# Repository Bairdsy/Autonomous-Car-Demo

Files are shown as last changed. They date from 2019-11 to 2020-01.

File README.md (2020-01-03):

# Automous Car Demo

SAS Computer Vision demo with 3d printed autonomous car platform.  The sub-folders in this repository contain everything you need to know to build the demo, other than the building of the models / preparation of the Astores.
  - Astore Switcher :  The GUI for swapping the Astore and restarting the ESP server
  - Car Code : The autonomous navigation code running on the vehicle
  - Control Code : The code running on the control Raspberry Pi, which manages the lights, monitors and sensors
  - Electronics : How to setup the Raspberry Pi Zero W, Explorer Phat, Operating System and required modules (e.g. mjpg streamer)
  - ESP Server:  Containing the deployment & install scripts for setting up the ESP server on a virtual machine
  - Hardware : Instructions for building the car model frame and chassis
  - Images : Images used in the instructions

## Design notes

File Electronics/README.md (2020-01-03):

#Electronics Setup & Install
## Raspberry Pi OS Install 
1. In a web browser, navigate to the URL http://downloads.raspberrypi.org/raspbian/images/raspbian-2018-11-15/ and download the zip file 2018-11-13-raspbian-stretch.zip
2. Download and install the latest version of Balena Etcher for your desktop operating system from https://www.balena.io/etcher/
3. Run Balena Etcher
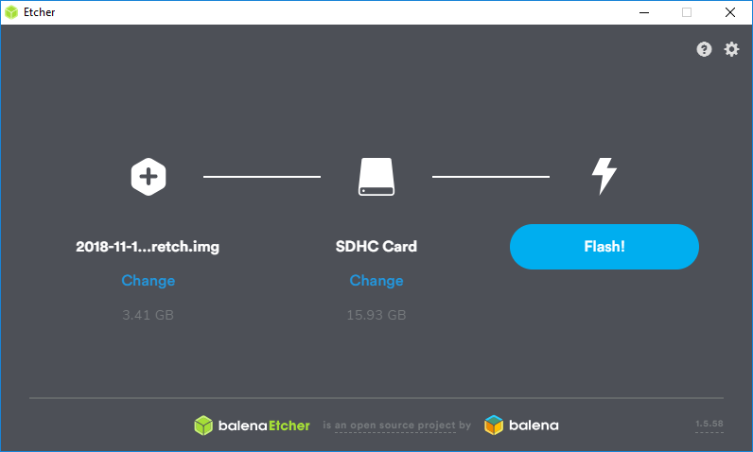
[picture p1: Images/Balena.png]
Etcher Screenshot
  
4. Click on “Select Image” and select the Raspbian Stretch zip file you downloaded.
5. Insert your microSD card into the slot on your computer (or a USB microSD reader if you don’t have a slot)
6. Click on “Flash!” 
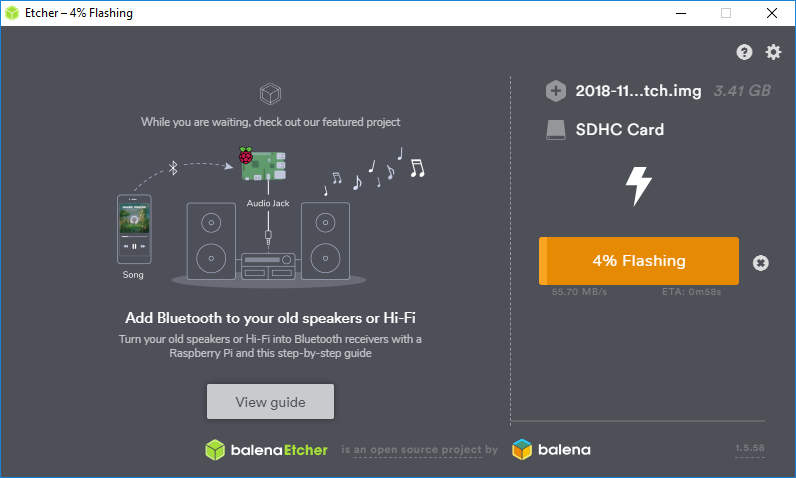
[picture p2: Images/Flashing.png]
Flashing
  
7. Wait for Balena Etcher to finish “Flashing” and “Verifying”.  Close any windows that pop up during this process giving warnings about drives that need formatting.
8. Remove the microSD card from your computer and insert it into the slot on the Raspberry Pi Zero W
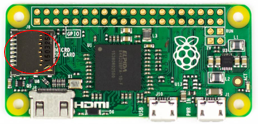
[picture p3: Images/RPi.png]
Raspberry Pi
  

## Explorer Phat
1.  The explorer Phat plugs into the top of the Raspberry Pi board as pictured
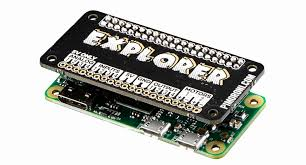
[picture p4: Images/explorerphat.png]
Explorer
  
2. Connect each of the 2 motors to the Motor 1 + and - and Motor 2 + and - connectors on the board
3. Connect the IR distance sensor to the Ground, Analog and 5V connectors

## Video Streaming Service
### Update & Install Tools
```
sudo apt-get update -y
sudo apt-get upgrade -y
sudo apt-get install build-essential imagemagick libv4l-dev libjpeg-dev cmake -y```
```

### Clone Repo in /tmp
```
cd /tmp
git clone https://github.com/jacksonliam/mjpg-streamer.git
cd mjpg-streamer/mjpg-streamer-experimental
```

### Make
```
make
sudo make install
```

### Run
```
/usr/local/bin/mjpg_streamer -i "input_uvc.so -r 1280x720 -d /dev/video0 -f 30" -o "output_http.so -p 8080 -w /usr/local/share/mjpg-streamer/www"
```

## Python Libraries
```
pip3 install scikit-learn
pip3 install scikit-image
sudo apt-get install python-opencv
sudo apt-get install python3-opencv
git clone http://github.com/pimoroni/explorer-hat
cd explorer-hat/library
sudo python setup.py install
```

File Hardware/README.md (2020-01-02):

# Hardware:
## Bill of Materials:
### For the Vehicle
| Number | Item | Indicative Cost |
| --- | --- | --- |
| 1 | Raspberry Pi Zero W (https://shop.pimoroni.com/products/raspberry-pi-zero-wh-with-pre-soldered-header) | $20.00 |
| 1 | Explorer Phat (https://shop.pimoroni.com/products/explorer-phat) | $17.00 |
| 1 | Pololu Zumo Chassis Kit (https://shop.pimoroni.com/products/zumo-chassis-kit-no-motors) | $31.00 |
| 2 | Micro Metal Gearmotor (https://shop.pimoroni.com/products/micro-metal-gearmotor-extended-back-shaft) – 50:1 or 298:1 (will impact speed) | 2 x $8.00 = $16.00 |
| 1 | 3D printed Inner Car Body (.STL 3D model included in GitHub)	| $10 (for filament) |
| 1 | 3D printed Outer Car Shell - Ambulance (.STL 3D model included in GitHub)	| $10 (for filament) |
| 1 | 3D printed Outer Car Shell - Mining Truck (.STL 3D model included in GitHub)	| $10 (for filament) |
| 1 | 3D printed Outer Car Shell - Van (.STL 3D model included in GitHub)	| $10 (for filament) |
| 1 | Power bank or battery pack capable of USB 5V 2A output – as small as possible | $20 |
| 1 | 16GB Micro SD Card | $10 |
| 1 | Sharp GP2Y0A21YK0F Reflective Sensor (https://au.rs-online.com/web/p/reflective-optical-sensors/6666564/) | $17 |
| 1 | USB to Micro USB cable (slimline, right anlge if possible) | $5
| 1 | Pkt Male to Male Jumper Jerky (https://shop.pimoroni.com/products/jumper-jerky-junior?variant=1076482173) | $4 |
| 1 | Camera module for Raspberry Pi Zero (https://shop.pimoroni.com/products/raspberry-pi-zero-camera-module) | $12 |

Estimated total cost:  $182

### For the Control Board, Monitor, Sensors & LEDs
| Number | Item | Indicative Cost |
| --- | --- | --- |
| 1 | Raspberry Pi 4 1GB (https://shop.pimoroni.com/products/raspberry-pi-4?variant=29157087379539) | $54 |
| 4 | Programmable RGB LEDs | 4 x $5 |	
| 1 | Explorer Hat Pro (https://shop.pimoroni.com/products/explorer-hat) | $31 |
| 4 | Force Sensing Resistor (https://core-electronics.com.au/search/?q=pololu-1645) | 4 x $14 |
| 1 | 7 inch monitor (or similar) | unknown |
		
Estimated total cost:  $157.00

### For the Enclosure
| Number | Item | Indicative Cost |
| --- | --- | --- |
| 2 | 900 x 1200 x 5mm Ply-Wood boards (white) | 2 x $11 |
| 8 | 3D printed corner brackets | $5 (for filament) |	
		
Estimated total cost:  $62.00

## Instructions:

### The Corner Brackets
The enclosure is held together by 3d printed corner brackets.  The STL model for these brackets is:
 - Double Bracket.stl

The original demo versions were printed on a Wanhao Duplicator i3 Plus in PLA with 0.14mm layer height.
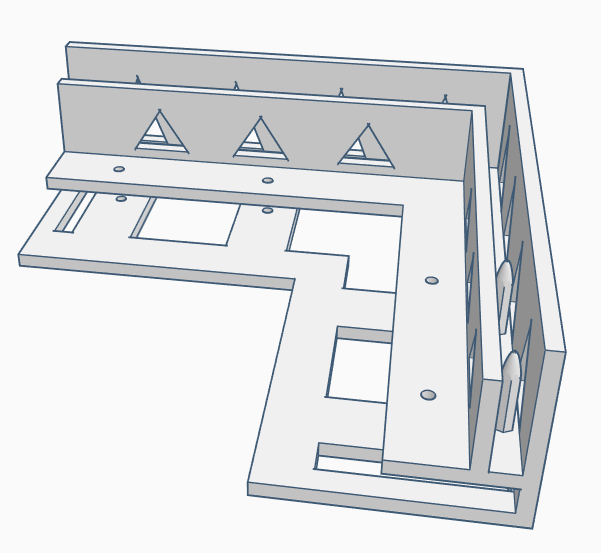
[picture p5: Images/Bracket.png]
Brackets
  

### Zumo Chassis Construction
1.	Check you have all components: 
  -	Zumo chassis main body
  -	1/16″ black acrylic mounting plate
  -	Two drive sprockets
  -	Two idler sprockets
  -	Two 22-tooth silicone tracks
  -	Two shoulder bolts with washers and M3 nuts
  -	Four 1/4″ #2-56 screws and nuts
  -	Battery terminals
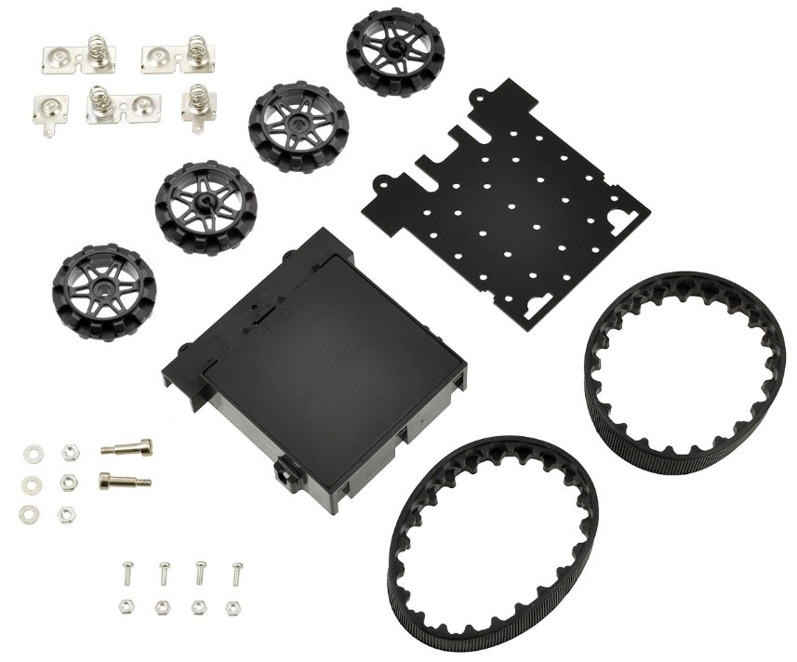
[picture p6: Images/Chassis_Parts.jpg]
Chassis Parts
  
2.	Place an M3 nut in each of the two side slots near the rear of the chassis. The slots are sized so that nuts will not be able to rotate within them
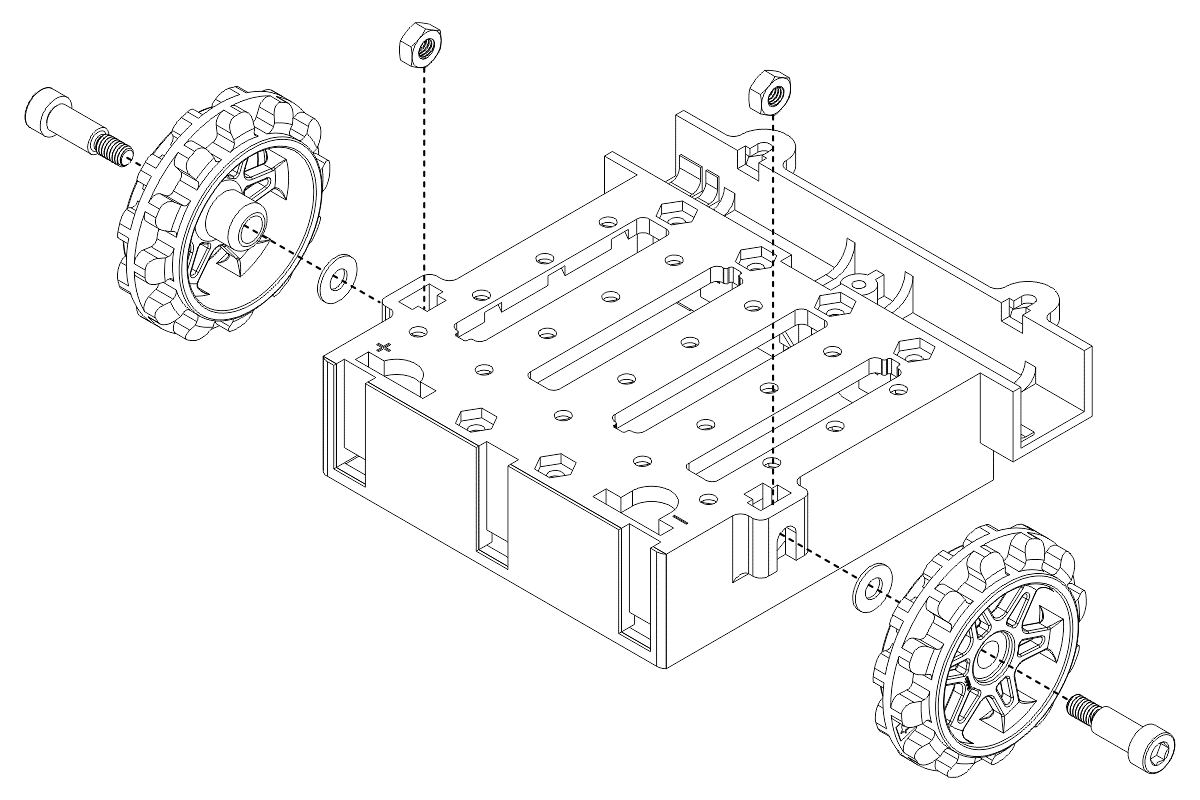
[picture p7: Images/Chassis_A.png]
Wheel Assembly
  
3.	Place an idler sprocket on each shoulder bolt, followed by a washer. The protruding side of the sprocket hub should face the same direction as the threaded end of the bolt (in toward the chassis).
4.	Insert the shoulder bolts through the side of the chassis into the nut. Use a 3 mm hex key (Allen wrench) to tighten the bolts until the washers are snug against the chassis. Be careful not to overtighten the shoulder bolts as doing so can bend the washers 
5.	Solder 2 wires from the jumper jerky onto the connectors for each of the 2 gear motors before installing the motors in the chassis, as you will not be able to access the motor leads easily once the acrylic mounting plate is in place.
6.	Press the output shafts of the motors into the drive sprockets, with the raised lip on one side of the sprocket facing away from the motor. The end of the gearbox shaft should end up flush with the outside of the sprocket. A good way to do this is to set the wheel on flat surface (like a table top) and press the motor shaft into the wheel until it contacts the surface.
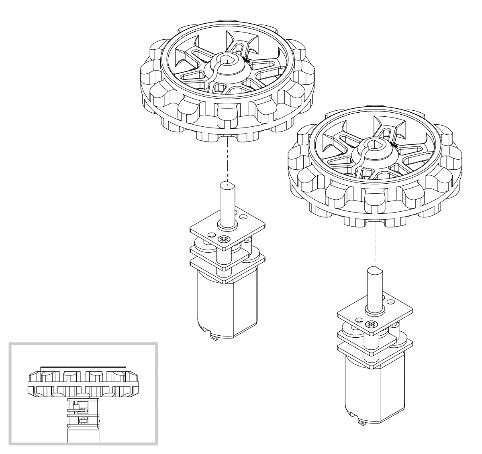
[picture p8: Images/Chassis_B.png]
  
7.	Place the motors into the channel in the front of  the chassis, aligning the gearbox with the grooves in the channel. The front plate of the gearbox should be even with the edge of the chassis.
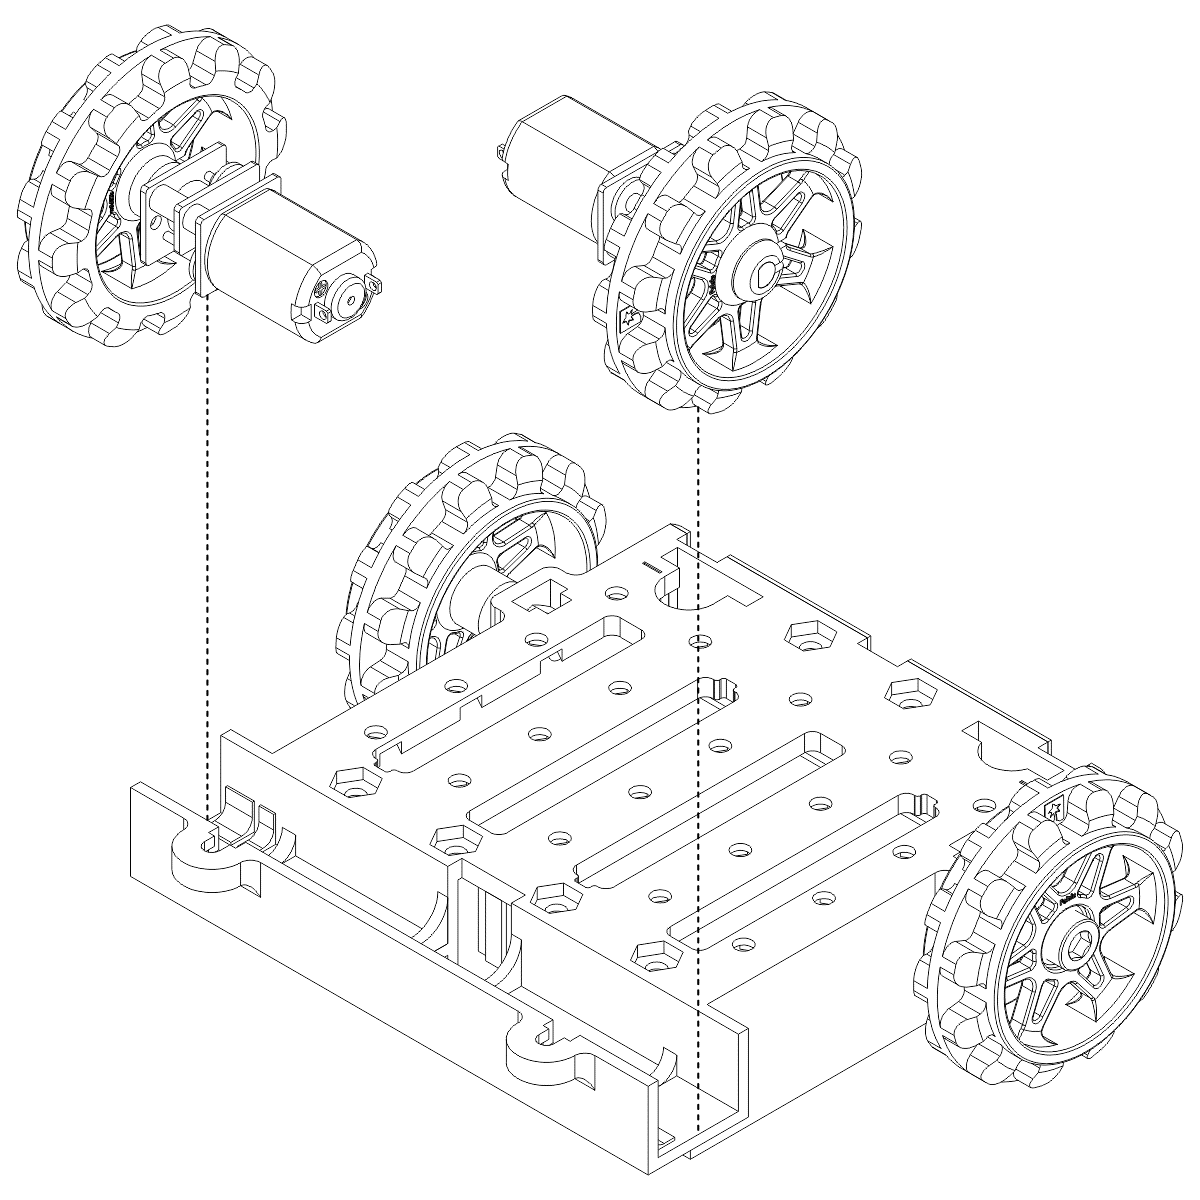
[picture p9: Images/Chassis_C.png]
  
8.	In each of the two front tabs and your choice of the interior-nut holes along the rear, insert a  machine screw through the mounting plate and chassis and tighten it against a nut inside the chassis. You can line up the nut by feel, or you could try temporarily taping the nuts inside the recesses in the chassis.
9.	Add the silicone tracks by stretching them around the sprockets on each side of the chassis.

### The Car Bodies
The STL files for the 3D models are available in this folder of the repository.  
 - Box Chassis.stl  :  The inner compartment of the car which houses the electronics
 - Box Chassis - Lid.stl : The lid to the inner compartment
 - Ambulance Vehicle Skin.stl : The Ambulance skin
 - Van shell.stl : The Delivery Van skin
 - Mining Truck Skin.stl : The Mining Truck skin 

The original demo versions were printed on a Wanhao Duplicator i3 Plus in PLA with 0.14mm layer height.
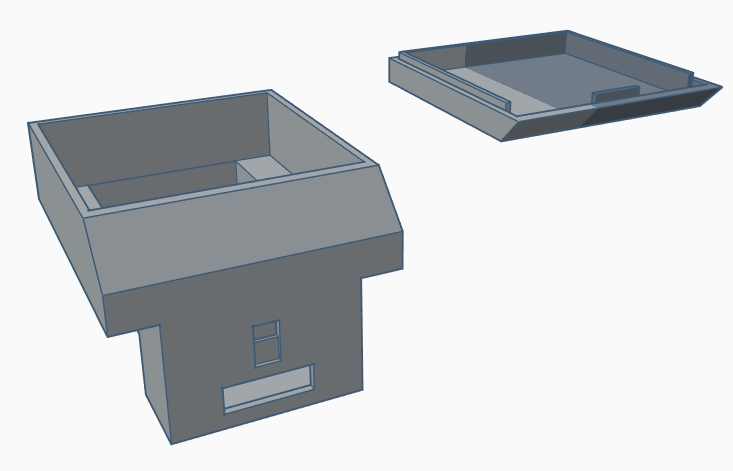
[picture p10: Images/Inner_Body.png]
InnerShell
  
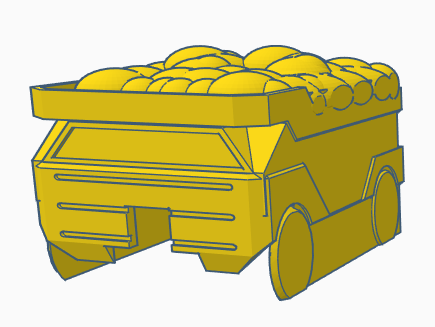
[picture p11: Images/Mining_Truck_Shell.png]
MiningTruck
  
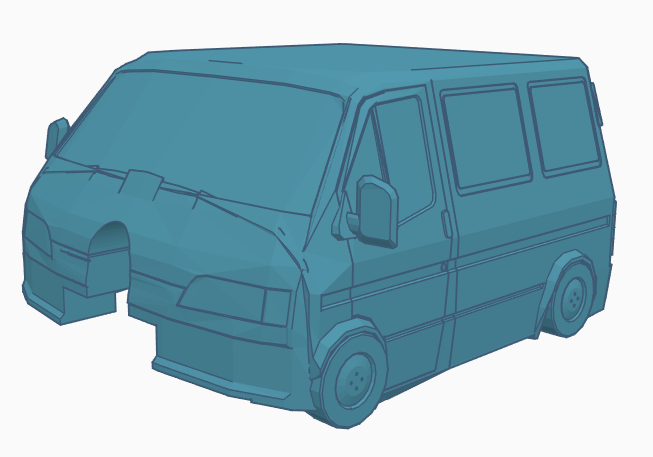
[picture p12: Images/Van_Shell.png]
VanShell
  
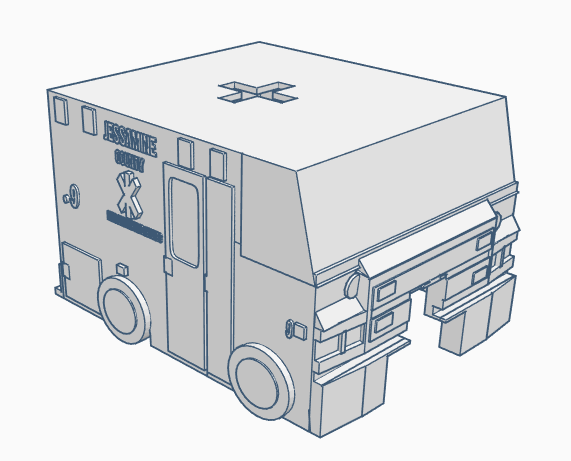
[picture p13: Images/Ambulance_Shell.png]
AmbulanceShell


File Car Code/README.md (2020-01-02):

# Autonomous Car Code
This is the code which controls the movement and actions of the autonomous vehicle.  It is responsible for:
  - Communicating with the ESP server to receive it's next instruction
  - Searching for, correctly identifying and driving towards the coloured LED
  - Avoiding obstacles and collision detection

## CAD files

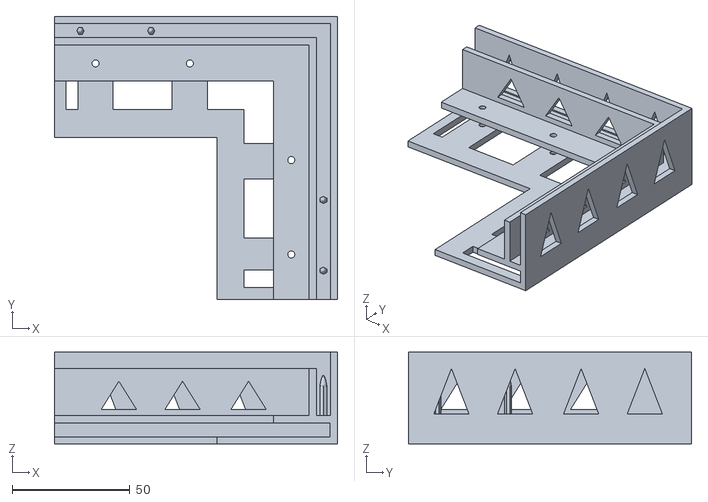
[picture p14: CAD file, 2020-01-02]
Hardware/Double Bracket.stl
120.0 x 120.0 x 39.0

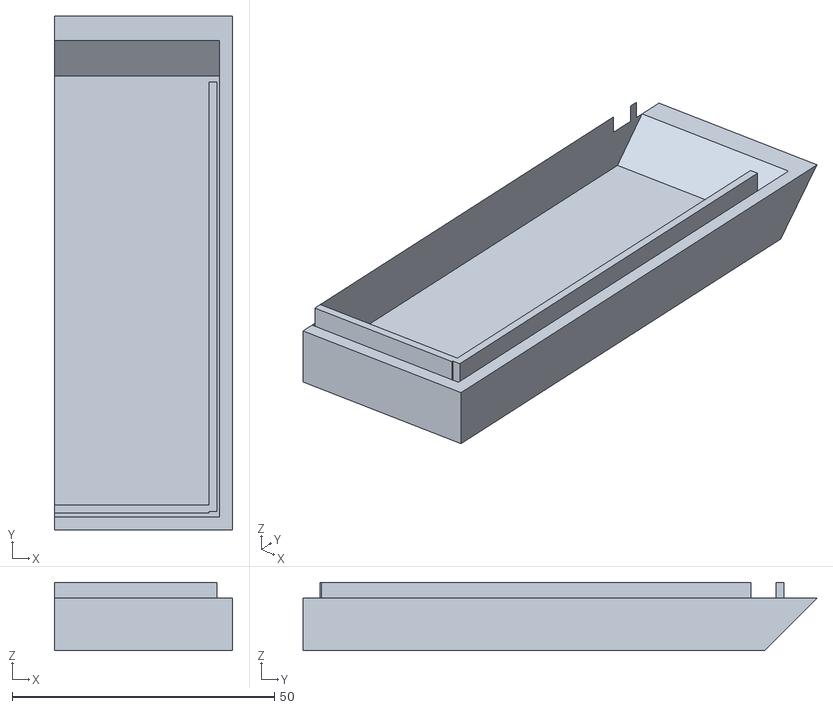
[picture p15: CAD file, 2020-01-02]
Hardware/Box Chassis - Lid.stl
34.0 x 98.0 x 13.0

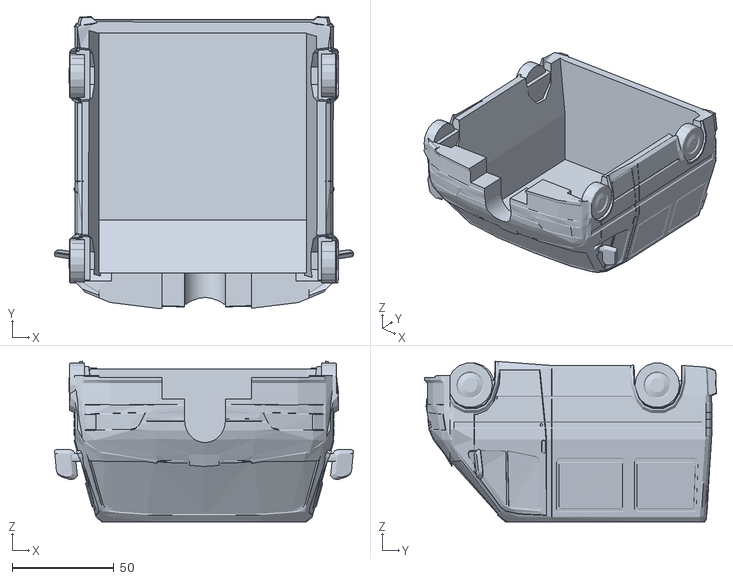
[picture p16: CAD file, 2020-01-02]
Hardware/Van shell.stl
147.0 x 143.5 x 79.0

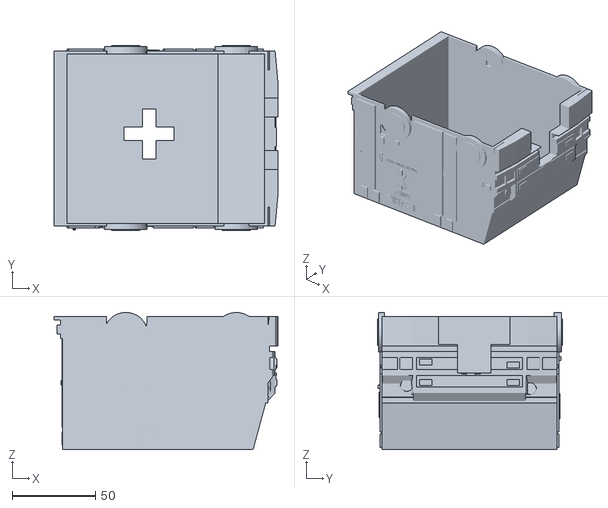
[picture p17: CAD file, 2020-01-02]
Hardware/Ambulance Vehicle Skin.stl
134.7 x 111.2 x 82.5

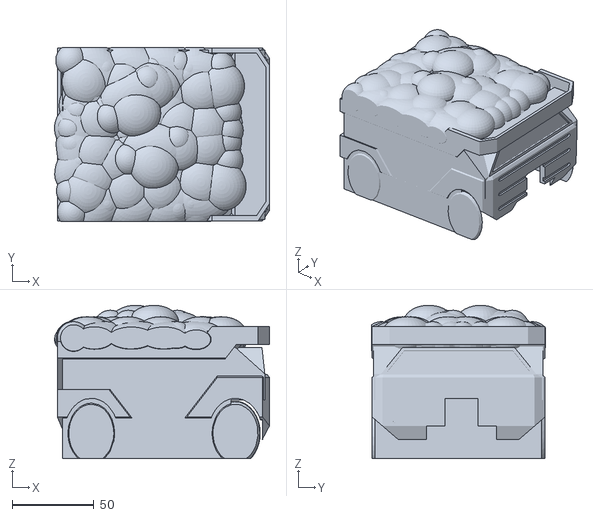
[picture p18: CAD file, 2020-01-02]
Hardware/Mining Truck Skin.stl
131.7 x 106.5 x 94.0

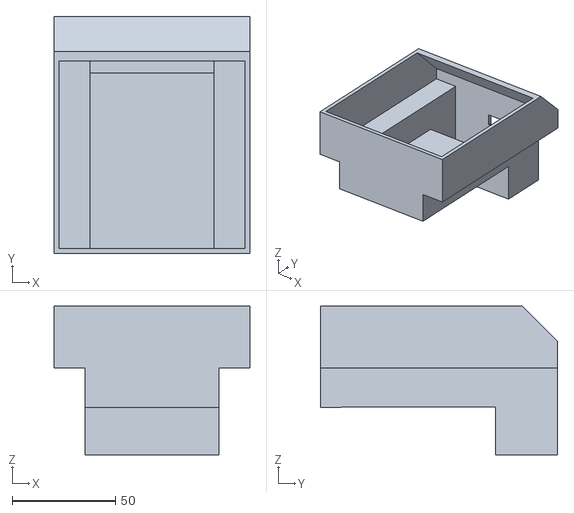
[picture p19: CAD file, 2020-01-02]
Hardware/Box Chassis.stl
95.0 x 115.0 x 72.0

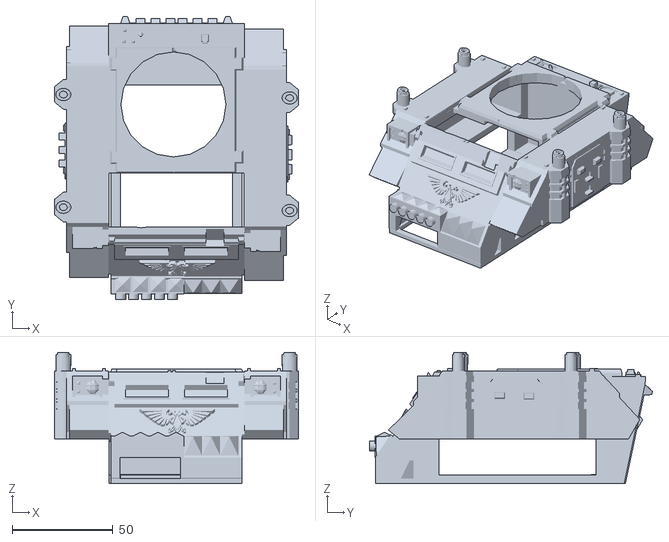
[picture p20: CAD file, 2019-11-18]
Hardware/Pi Zero Tank.stl
121.0 x 140.1 x 65.1

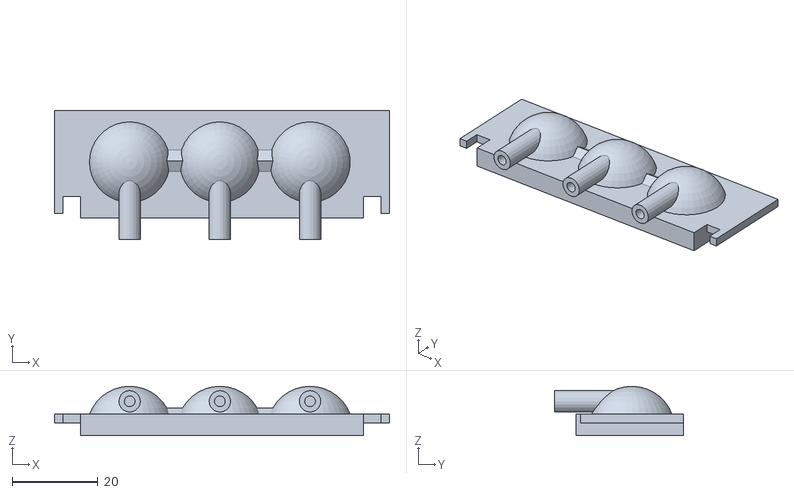
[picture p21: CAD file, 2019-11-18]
Hardware/Pi Zero Tank Guns.stl
78.0 x 30.0 x 11.5

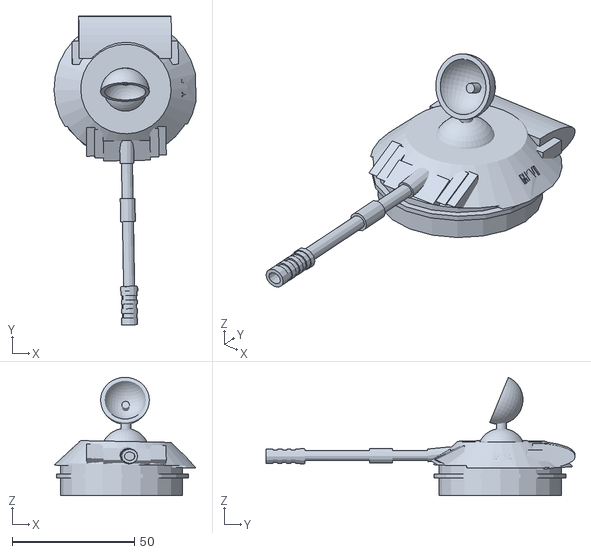
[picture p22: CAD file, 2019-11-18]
Hardware/Pi Zero Tank Turret.stl
58.0 x 126.3 x 48.3

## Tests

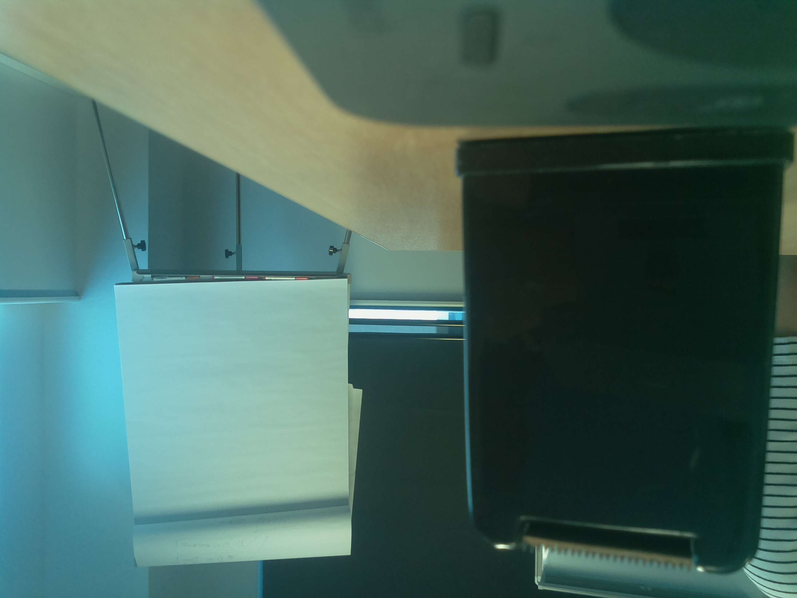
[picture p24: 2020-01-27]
Car Code/stream/mjpg-streamer/mjpg-streamer-experimental/test.jpg

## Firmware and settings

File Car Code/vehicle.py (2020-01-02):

#!/usr/bin/python3
 
import sys, termios, tty, os, time
import explorerhat
import numpy as np
import cv2
import glob


def getch():
    fd = sys.stdin.fileno()
    old_settings = termios.tcgetattr(fd)
    try:
        tty.setraw(sys.stdin.fileno())
        ch = sys.stdin.read(1)
    finally:
        termios.tcsetattr(fd, termios.TCSADRAIN, old_settings)
    return ch

def image_average(img):
    average = img.mean(axis=0).mean(axis=0)
    return average

def image_max(img):
    average = img.max(axis=0).max(axis=0)
    return average


def image_crop(img, x, y, h, w):
    crop_img = img[y:y+h, x:x+w]
    return crop_img

def RGB2HEX(color):
    return "#{:02x}{:02x}{:02x}".format(int(color[0]), int(color[1]), int(color[2]))

def get_image(image_path):
    image = cv2.imread(image_path)
    image = cv2.cvtColor(image, cv2.COLOR_BGR2RGB)
    return image

def convert_to_HSV(img):
    out_img = cv2.cvtColor(img,cv2.COLOR_RGB2HSV)
    return out_img


button_delay = 0.4
speed = 30

while True:
    print("Vehicle is ready for input:")
    char = getch()
 
    if (char == "p"):
        print("Exit!")
        exit(0)

    elif (char == "f"):
        print("Faster pressed")
        speed = speed + 5
        if (speed > 100):
            speed = 100
        print(" Speed set to ",speed)

    elif (char == "v"):
        print("Slower pressed")
        speed = speed - 5
        if (speed < 5):
            speed = 5
        print(" Speed set to ",speed)
    
    elif (char == "a"):
        print("Left pressed")
        explorerhat.motor.two.backwards(speed)
        explorerhat.motor.one.forwards(speed)
        time.sleep(button_delay)
 
    elif (char == "d"):
        print("Right pressed")
        explorerhat.motor.two.forwards(speed)
        explorerhat.motor.one.backwards(speed)
        time.sleep(button_delay)
 
    elif (char == "w"):
        print("Up pressed")
        explorerhat.motor.one.forwards(speed)
        explorerhat.motor.two.forwards(speed)
        time.sleep(button_delay)
 
    elif (char == "s"):
        print("Down pressed")
        explorerhat.motor.one.backwards(speed)
        explorerhat.motor.two.backwards(speed)
        time.sleep(button_delay)
 
    elif (char == "x"):
        print("STOP pressed")
        explorerhat.motor.one.stop()
        explorerhat.motor.two.stop()
        time.sleep(button_delay)

    elif (char == "e"):
        print("READ SENSOR pressed")
        sensor = explorerhat.analog.one.read()
        print("value = %f",sensor)
        time.sleep(button_delay)

    elif (char == "n"):
        print("AUTO-NAVIGATE")
        lastreading = 99999
        samecount = 0
        for i in range(500):
            print(" iteration ",i)
            reading = explorerhat.analog.one.read()
            if ( reading - lastreading < 0.1 and lastreading - reading < 0.1):
                samecount = samecount + 1
                if ( samecount > 5 ):
                    print("STUCK - reversing")
                    explorerhat.motor.one.backwards(100)
                    explorerhat.motor.two.backwards(100)
            else:
                samecount = 0

            if (reading > 1.8):
                print("Obstruction detected - turn")
                if ( int(i / 100) % 2 == 0):
                    explorerhat.motor.one.backwards(speed)
                    explorerhat.motor.two.forwards(speed)
                else:
                    explorerhat.motor.two.backwards(speed)
                    explorerhat.motor.one.forwards(speed)
                time.sleep(0.25)
            else:
                print("No obstruction - forward")
                explorerhat.motor.one.forwards(speed)
                explorerhat.motor.two.forwards(speed)
            time.sleep(0.25)
        explorerhat.motor.one.stop()
        explorerhat.motor.two.stop()
        time.sleep(button_delay)

    elif (char == "q"):
        print("PHOTO pressed")
        image_file = time.strftime("/home/pi/Images\/%Y-%m-%d-%H-%M-%S.jpg")
        cmd = "raspistill -rot 180 -w 640 -h 480 -o " + image_file
        os.system(cmd)
        print("PHOTO done")
        time.sleep(button_delay)

    elif (char == "b"):
        print("FINDING BLUE LIGHT")
        vidcap = cv2.VideoCapture('http://127.0.0.1:8080/?action=stream')
        success,image = vidcap.read()
        count = 0
        while (success) and (count < 40):
            count = count + 1
            print("iteration " + str(count) + "of 40")#, end =",")
            vidcap = cv2.VideoCapture('http://127.0.0.1:8080/?action=stream')
            success,image = vidcap.read()
            cropped = image_crop(image,0,100,180,640)
            average = image_max(cropped)
            #print(average, end=",")
            #print(average[2], end=",")

            if (average[2] >= 254):
                gray = cropped[:,:,0]
                gray = cv2.GaussianBlur(gray, (3, 5), 0)
                (minVal, maxVal, minLoc, maxLoc) = cv2.minMaxLoc(gray)
                cv2.circle(cropped, maxLoc, 20, (255, 0, 0), 2)
               
                #print("Colour loc is")
                #print(maxLoc, end=",")
                motor_ratio = 1 + ((maxLoc[0]-320)/200)
                #print(motor_ratio, end=",")
                newspeed = speed * motor_ratio
                if (newspeed > 100):
                    newspeed = 100
                if (newspeed < 0):
                    newspeed = 0
                #print(newspeed, end=",")
                explorerhat.motor.one.forwards(speed)
                explorerhat.motor.two.forwards(newspeed)

            else:
                #print("Colour not found.  Turning", end=",")
                explorerhat.motor.one.forwards(speed)
                explorerhat.motor.two.backwards(speed)
                time.sleep(button_delay)
                explorerhat.motor.one.stop()
                explorerhat.motor.two.stop()
            #print()
            filename = "{:03}:".format(count)+".jpg"
            cv2.imwrite(filename, cropped)
        explorerhat.motor.one.stop()
        explorerhat.motor.two.stop()

    elif (char == "r"):
        print("FINDING RED LIGHT")
        vidcap = cv2.VideoCapture('http://127.0.0.1:8080/?action=stream')
        success,image = vidcap.read()
        count = 0
        while (success) and (count < 40):
            count = count + 1
            print("iteration " + str(count) + "of 40")#, end =",")
            vidcap = cv2.VideoCapture('http://127.0.0.1:8080/?action=stream')
            success,image = vidcap.read()
            cropped = image_crop(image,0,100,180,640)
            average = image_max(cropped)
            #print(average, end=",")
            #print(average[0], end=",")

            if (average[0] >= 254):
                gray = cropped[:,:,2]
                gray = cv2.GaussianBlur(gray, (3, 5), 0)
                (minVal, maxVal, minLoc, maxLoc) = cv2.minMaxLoc(gray)
                cv2.circle(cropped, maxLoc, 20, (0, 0, 255), 2)
               
                #print("Colour loc is")
                #print(maxLoc, end=",")
                motor_ratio = 1 + ((maxLoc[0]-320)/200)
                #print(motor_ratio, end=",")
                newspeed = speed * motor_ratio
                if (newspeed > 100):
                    newspeed = 100
                if (newspeed < 0):
                    newspeed = 0
                #print(newspeed, end=",")
                explorerhat.motor.one.forwards(speed)
                explorerhat.motor.two.forwards(newspeed)

            else:
                #print("Colour not found.  Turning", end=",")
                explorerhat.motor.one.forwards(speed)
                explorerhat.motor.two.backwards(speed)
                time.sleep(button_delay)
                explorerhat.motor.one.stop()
                explorerhat.motor.two.stop()
            #print()
            filename = "{:03}:".format(count)+".jpg"
            cv2.imwrite(filename, cropped)
        explorerhat.motor.one.stop()
        explorerhat.motor.two.stop()
        
    elif (char == "g"):
        print("FINDING GREEN LIGHT")
        vidcap = cv2.VideoCapture('http://127.0.0.1:8080/?action=stream')
        success,image = vidcap.read()
        count = 0
        while (success) and (count < 40):
            count = count + 1
            print("iteration " + str(count) + "of 40")#, end =",")
            vidcap = cv2.VideoCapture('http://127.0.0.1:8080/?action=stream')
            success,image = vidcap.read()
            cropped = image_crop(image,0,100,180,640)
            average = image_max(cropped)
            #print(average, end=",")
            #print(average[0], end=",")

            if (average[1] >= 254):
                gray = cropped[:,:,1]
                gray = cv2.GaussianBlur(gray, (3, 5), 0)
                (minVal, maxVal, minLoc, maxLoc) = cv2.minMaxLoc(gray)
                cv2.circle(cropped, maxLoc, 20, (0, 255, 0), 2)
               
                #print("Colour loc is")
                #print(maxLoc, end=",")
                motor_ratio = 1 + ((maxLoc[0]-320)/200)
                #print(motor_ratio, end=",")
                newspeed = speed * motor_ratio
                if (newspeed > 100):
                    newspeed = 100
                if (newspeed < 0):
                    newspeed = 0
                #print(newspeed, end=",")
                explorerhat.motor.one.forwards(speed)
                explorerhat.motor.two.forwards(newspeed)

            else:
                #print("Colour not found.  Turning", end=",")
                explorerhat.motor.one.forwards(speed)
                explorerhat.motor.two.backwards(speed)
                time.sleep(button_delay)
                explorerhat.motor.one.stop()
                explorerhat.motor.two.stop()
            #print()
            filename = "{:03}:".format(count)+".jpg"
            cv2.imwrite(filename, cropped)
        explorerhat.motor.one.stop()
        explorerhat.motor.two.stop()

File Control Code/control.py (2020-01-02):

#!/usr/bin/env python3

import time
from neopixel import *

# LED strip configuration:
LED_COUNT      = 3      # Number of LED pixels.
LED_PIN        = 18      # GPIO pin connected to the pixels (18 uses PWM!).
#LED_PIN        = 10      # GPIO pin connected to the pixels (10 uses SPI /dev/spidev0.0).
LED_FREQ_HZ    = 800000  # LED signal frequency in hertz (usually 800khz)
LED_DMA        = 10      # DMA channel to use for generating signal (try 10)
LED_BRIGHTNESS = 204     # Set to 0 for darkest and 255 for brightest
LED_INVERT     = False   # True to invert the signal (when using NPN transistor level shift)
LED_CHANNEL    = 0       # set to '1' for GPIOs 13, 19, 41, 45 or 53


# Define functions which animate LEDs in various ways.
def colorWipe(strip, color, wait_ms=50):
    """Wipe color across display a pixel at a time."""
    for i in range(strip.numPixels()):
        strip.setPixelColor(i, color)
        strip.show()
        time.sleep(wait_ms/1000.0)


# Main program logic follows:
if __name__ == '__main__':

    # Create NeoPixel object with appropriate configuration.
    strip = Adafruit_NeoPixel(LED_COUNT, LED_PIN, LED_FREQ_HZ, LED_DMA, LED_INVERT, LED_BRIGHTNESS, LED_CHANNEL)
    # Intialize the library (must be called once before other functions).
    strip.begin()

    try:

        while True:
            light = input("select LED (0-2):")
            red   = input("enter RED amount (0-255):")
            blue  = input("enter BLUE amount (0-255):")
            green = input("enter GREEN amount (0-255):")
            strip.setPixelColor(light, Color(green,red,blue))
            strip.show()

    except KeyboardInterrupt:
        colorWipe(strip, Color(0,0,0), 10)
